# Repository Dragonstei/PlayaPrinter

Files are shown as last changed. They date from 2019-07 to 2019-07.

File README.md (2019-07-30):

# Playa Printer
You can find our project on: https://playaprinter.stadslabrotterdam.nl/

## The Idea

5 years ago Arnold Roosch, then a lab manager at Stadslab Rotterdam, came up with the idea to build a huge 3D dust printer to print objects out of sand at Burning Man Festival. Unfortunately, he wasn’t able to finish his project due to illness. Stadslab Rotterdam decided to continue the building of the printer with the help from friends and family of Arnold, lab employees and students from Rotterdam University of Applied Sciences.

## The Playa Printer

We aim to build a 3D sand printer to create sculptures that can be fully degraded and upcycled after a few days. The “Leave-no-trace” principle of Burning Man Festival is our inspiration. At the International FabLab Conference (FAB15) in Egypt we will be printing with desert sand. Because of the heat and wind the sculptures will dissolve in a few days. 

It is an ongoing project that will be improved and used with different materials by different groups of students.

### Resources:
* https://reprap.org/wiki/RAMPS_1.4
* http://www.geeetech.com/wiki/index.php/Ramps1.4

### Technical information:

Printer unique ID:
6b82af56-c7b9-41e2-99fa-451697f835ac

Stepper motor pin layout (A4988):\
2B = Black\
2A = Green\
1A = Red\
1B = Blue

**Make sure to redefine the steppermotor in configuration.h!**\

**Currently obsolete, printer does not have a screen connected**\
Make sure to download the latest NewLiquidCrystal library here and include it in Arduino:\
https://bitbucket.org/fmalpartida/new-liquidcrystal/downloads/

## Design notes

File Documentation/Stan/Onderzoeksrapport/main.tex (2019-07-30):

\documentclass[12pt, a4paper]{article}

\usepackage[english]{babel}
\usepackage[utf8]{inputenc}

% Skip to next paragraph on whiteline
\usepackage{parskip}

% Define bounds where text can be drawn
%\usepackage[top=100pt,bottom=100pt,left=75pt,right=75pt]{geometry}

% Headings
\usepackage{fancyhdr}
\pagestyle{fancy}
\fancyhf{}
\lhead{Research Playa Printer}
\rfoot{Page \thepage}

% Colors and links
\usepackage{color}
\definecolor{blue}{rgb}{0,0.5,1}
\usepackage{hyperref}
\hypersetup{
	colorlinks = true,
	linkcolor = blue,
	urlcolor = blue,
	citecolor = blue,
}

% Enable images
\usepackage{graphicx}
\usepackage{float}
\graphicspath{{images}{../images/}}

% Bibliography package
\usepackage[numberedbib]{apacite}
\bibliographystyle{apacite}

% Load LaTeX subfiles
\usepackage{import}
\usepackage{subfiles}
\usepackage[subpreambles=true]{standalone}

% Titlepage
\title{\textbf{Research paper Playa Printer\\Project 7/8}}
\author{Stan Boer, 0931006}
\date{\today}

%Examples:
%This is an example citation \cite{example}

\begin{document}
	\clearpage
	\maketitle
	\thispagestyle{empty}
	\newpage

	\setcounter{page}{1}
	\newpage
	
\section{Summary}
The aim of this research paper is to take a closer look at the options to automate the process of mixing clay and supplying that to our 3D printer. This to eradicate the manual labour and constant monitoring required for operating the printer.

To look at our available options, we'll take a look at what other companies, such as WASP and Italian inventor Enrico Dini, have accomplished in the process of building their own printers. Community made printers are based on manually mixing their materials and putting those in containers, so this is something that will not be covered in this research.

At the end of this paper we will elaborate on our findings, and explain why our goal is not achievable within our current scope.
	\newpage
	
	\tableofcontents
	\newpage
	
\section{Introduction}
The initial goal for the project is to build a 3D printer which will be able to print with a mixture that consists out of sand and a form of glue or epoxy, the Playa Printer. The plan with the current prototype is to print with a self-made clay mixture, as this is the most accessible to us. This mixture has to be made either by hand or be mixed by a machine. This second option would eliminate the effort required to mix the clay ourselves. This machine is supposed to be constantly running, getting the clay mixture ready to be transported to the extruder. This will eliminate the need to manually refill the printer every time the extruder is out of clay.

As this is a far more convenient option for a printer of our scale, we'll be looking into options on how to tackle this idea. This research paper will cover what options there are, show research done on the subject and a conclusion in which we will decide what prototype to build.
\begin{figure}[H]
	\centering
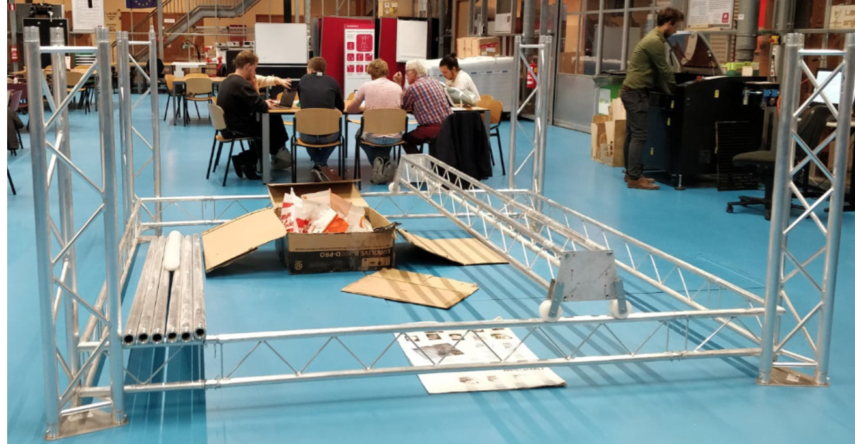
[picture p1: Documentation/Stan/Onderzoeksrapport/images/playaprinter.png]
	
	\caption{Playa Printer}
\end{figure}
	\newpage

\section{Research}
As the size of the printer is 3 by 3 meters, we will be needing a lot of material to be able to print at a scale like that. With existing 3D sand printers, the current method is to fill containers with the required mixture to be able to print with, and replace it every time the container is empty. For our project this can become quite inconvenient, which is why we will look in to figuring out a way of making this process more accessible. 
	
A company which created a similar 3D printer to ours, is called WASP. (reference) They created the Big Delta 3D printer, designed to be able to print with locally available materials at low cost. Their materials include mud combined with straw, and they are looking into the option to print with clay. They use a pugmill to combine their materials to be used as filament. When the extruder is empty, by the looks of it, the material has to be manually put into the extruder so that it can print again.
	
Unfortunately, there aren't any other companies working on a 3D printer of this scale. There are quite a few community made clay printers on small scale, so we can use that as a resource. Our aim will be to find a way to automatically mix our material together, and preferably pushes that to the extruder without requiring manual labour. The only effort required is to keep refilling the materials for the mixer. This situation would be close to ideal compared to what we are aiming for.

\section{Methodology}
Since 3D printing is picking up a lot of popularity, a lot more resources are available to us to develop a system on our down. To start, we'll have to look in to a different options on how to automate our mixing. Secondly, we'll have to compare the options, and pick one which we'll design a prototype for. 

To do an available product analysis, we'll be looking at the Big Delta printer from WASP and other companies who have attempted printing with sand. As the Big Delta printer is quite similar in design, it can be helpful in deciding our path to take. We'll be putting more priority on this specific printer than the other options. This will later be elaborated in the results.
	\newpage

\section{Results}
\subsection{Types of mixers}
\textbf{Hopper mixer}

Hopper mixers are an adaptation to mixers used for dough mixing, which consists of a horizontal shaft and either an open or lidded hopper. With this kind of mixer, dry material has to be added first and the liquid second. Some of thse mixers have the option to reverse the direction of the blades, so complete mixing can be achieved. Afterwards, the mixed clay has to be removed by hand and put in to the extruder.
\begin{figure}[H]
	\centering
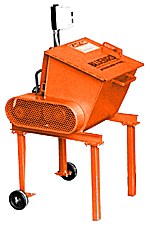
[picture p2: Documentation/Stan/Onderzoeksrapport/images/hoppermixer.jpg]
	
	\caption{Hopper mixer}
\end{figure}
	\newpage

\textbf{Soldner mixer}

Another form of mixers is a Soldner mixer, named after its designer. This mixer consists of a chain-driven rotating tub, with stationary bars on the inside, which allows the mixture to blend quickly and effectively. With this mixer it's normal to add the liquid first. After the dry material is added, it will be rotated through the stationary bars which chops and blends the clay for the desired consistency. This mixer also requires the material to be unloaded manually by hand and then stored.
\begin{figure}[H]
	\centering
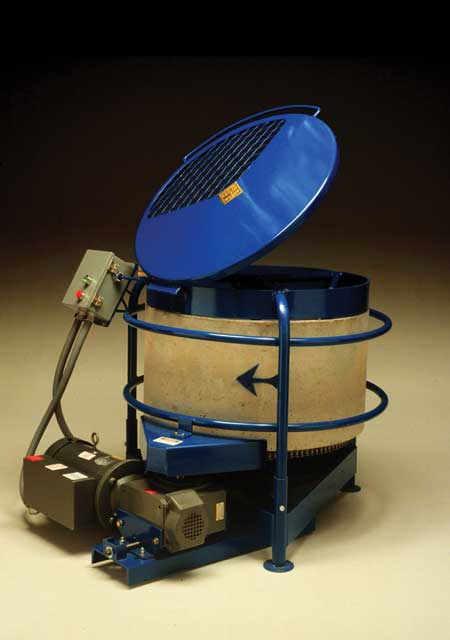
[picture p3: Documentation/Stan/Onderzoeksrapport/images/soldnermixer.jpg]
	
	\caption{Soldner mixer}
\end{figure}
	\newpage

\textbf{Pugmill}

Pugmills also work through a hopper and make use of a horizontal bladed shaft. The pugmill mixer requires moist clay to be put into the hopper which after blending gets extruded to a restricted opening at the end of a barrel. That means we are required to mix our material beforehand, which defeats the purpose of automating our process. Pugmills have the option to be equipped with a de-airing vacuum that can produce clay that is ready to be used, so that does give us an option of automation at the end of the process. 
\begin{figure}[H]
	\centering
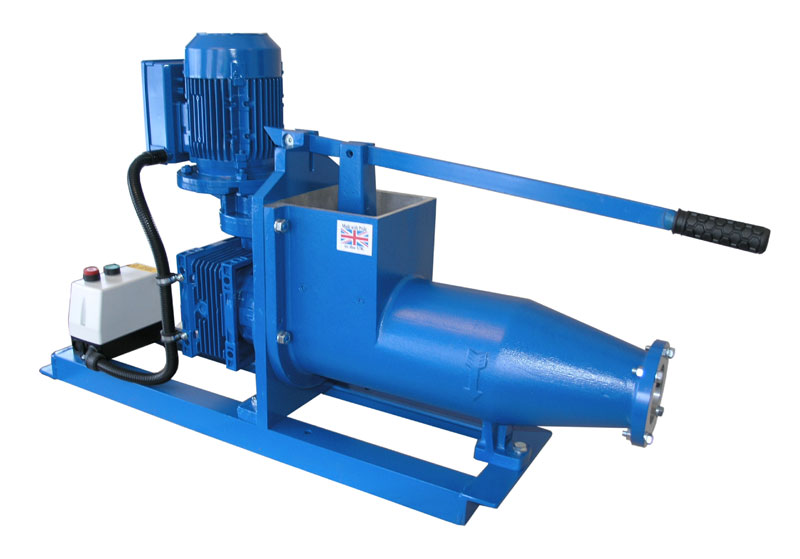
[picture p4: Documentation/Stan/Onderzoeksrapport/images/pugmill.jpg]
	
	\caption{Pugmill}
\end{figure}
	\newpage

\textbf{Mixer/pugmill}

Mixer/Pugmill combinations allow for both mixing clay and having a separate extruder for the material. The pugmill portion can serve as a discharge unit for the mixer, or as a separate pugmill on its own. The option of having a de-airing accessory will make it easier for us to automate the process of refilling the extruder.
\begin{figure}[H]
	\centering
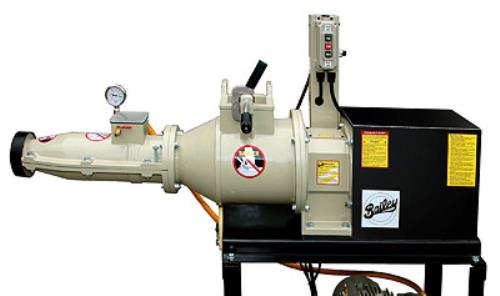
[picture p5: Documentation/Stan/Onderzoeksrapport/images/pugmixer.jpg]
	
	\caption{Mixer/pugmill combination}
\end{figure}
	\newpage

\subsection{Available printers}
To compare our available options, it is smart to look at what methods other companies use for their printers. Since there are only a few companies to look at, and most of them dont have their own resources available to us, our resources are quite limited to what we can find.

\textbf{Big Delta}

For our first example we will be looking at the Big Delta printer from WASP. They have built a 12 meter high printer, which they can use to print from locally available materials at low cost. Not much is known about their extruder. What is known just from pictures and videos from their demonstrations, is that they make use of an older pugmill. This mixer requires materials to be added to the machine, where it just keeps mixing the materials together untill it's ready for the extruder. It is also shown that the extruder needs to be manually refilled everytime, which can be quite some effort considering how high the printer can go.
\begin{figure}[H]
	\centering
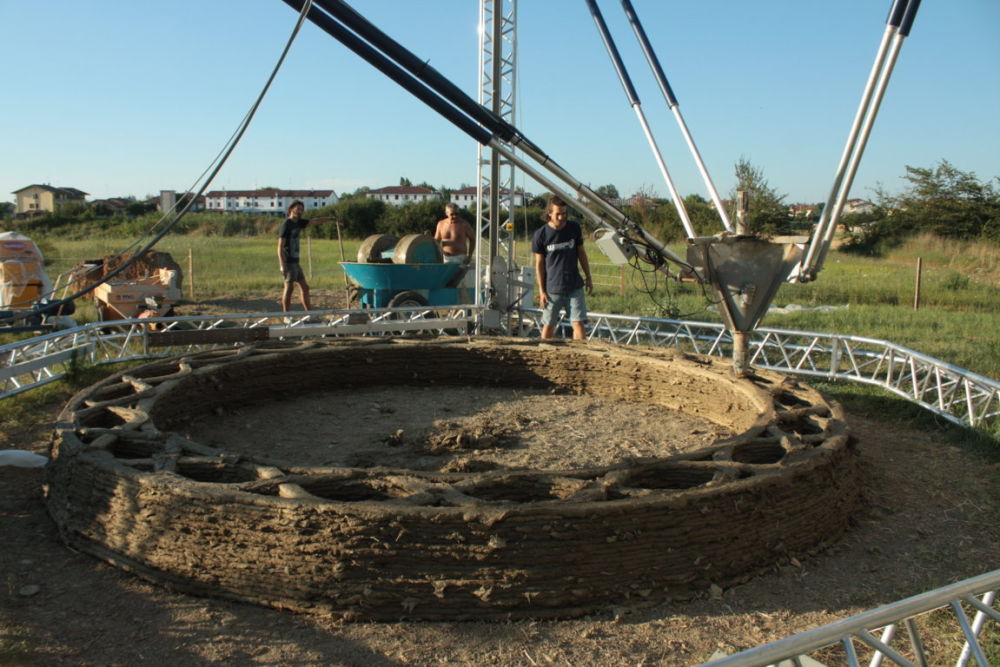
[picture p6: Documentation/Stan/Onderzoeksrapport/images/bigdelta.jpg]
	
	\caption{Big Delta printer using an older pugmill}
\end{figure}

This means that using an old hopmill and refilling manually still remaings one of our options, which is not really what we are looking for. It is unfortunate that they haven't gone towards automating this process, but this might still be a possibility for one of their future designs.
	\newpage
	
\textbf{D-Shape}
	
The D-Shape is a different kind of printer used than what we are working towards. This printer is effectively an up-scaled binder jetting process, where a binding material is dropped on each layer of powdered material. This method of printing is quite different than most orthodox 3D printers these days, is not really commercially available and would require us to completely rebuild our printer from scratch.
\begin{figure}[H]
	\centering
	
	\caption{D-Shape printer}
\end{figure}

Even though the frame is a lot more similar to our design compared to the Big Delta printer, the concept used for this printer is unfortunately not an option for us. The way this printer is controlled might be a point of interest for us, but for the sake of this research we will not be looking deeper into this. Development on the D-Shape has not been progressing a whole lot from what we know, so it's not worth to continue spending time on this printer for now.
	\newpage

\subsection{Comparison}
Now that we have our options listed and given a brief overview of what every mixer is capable of, it's time to put this in a morphological chart. This will help us in deciding which machine works best for our prototype. Since it is of no importance to us if we make use of a horizontal or vertical mixing shaft, we'll be leaving this out of our chart.

Because there are not really any available solutions for us to automate this process, we will have to come up with something ourselves based on the information gathered. That's why we'll only be looking at the side of automating our mixing process.

	\begin{tabular}{ | p{3.2cm} || p{2cm} | p{2cm} | p{2cm}| p{2.6cm} | }
	\hline
	\multicolumn{5}{|c|}{\textbf{Morphological chart}} \\
	\hline
	\textbf{Type} & Hopper mixer& Soldner mixer & Pugmill & Mixer/Pugmill \\
	\hline
	\textbf{Material} & Dry/ Wet & Dry/ Wet & Wet only & Dry/ Wet \\
	\hline
	\textbf{Starting price} & \$2,000  & \$6,000 & \$2,500 & \$5,000  \\
	\hline
	\textbf{De-airing} & No & No & Yes/No & Yes/No \\
	\hline
	\textbf{Unloading} & Manually & Manually & Manually/ Automatic & Manually/ Automatic \\ 
	\hline
	\end{tabular}

It remains quite difficult to make a proper comparison between our available options, as they are quite limited. We know that each one of these options gets the job done, but the focus remains on the unloading part. Preferably, we want the option to work with both dry and wet material, as we do not know beforehand what local materials are available. Any form of de-airing is welcome, as it will allow us to make the unloading and reloading into the extruder much more accessible.
	\newpage

\section{Conclusion}
Unfortunately, based on our research, the option to automatically refill containers is going to remain quite difficult. All of the available mixers still require manual unloading, while a few have the option to build an automatic system to refill on our own and attach it to the machine. Based on the scale of the printer and the scale of building such a system ourself, it is not smart to pursue this option for now. 

Since it is only the first protoype of this printer, it will become quite more difficult with the addition of a lot of moving parts, which can all influence the quality of the print and the weight of the printer itself. The option to manualy refill containers still remains, as the containers we use can be custom made with an adapter designed by ourselves. This should be done in combination with a de-airing unit, as this would immedietly get the material ready to be put into the containers.

Because of the price of these machines, it will be quite difficult for us to afford one. Our only options are that we either get one sponsored, or that we build one from scratch ourselves. Designing one would take a lot of research on its own, so it is best to pursue this at a later point in development if time permits.

No matter if we can get access to any of these mixers, or design one on our own, it is most advisable to look at a mixer/pugmill combination. A normal pugmill only works with wet material, which does not accomplish what we want to do. Both a hopper mixer and a Soldner mixer do not have the option of de-airing, which also defeats the purpose of our goal. Since we do not have a budget for buying one, we will start designing a prototype of a mixer/pugmill combination, to see what our options are and to see if we can accomplish the mixing on our own without having to make a huge investment.
	\newpage

	\nocite{*}
	\bibliography{main}
	\newpage

\end{document}

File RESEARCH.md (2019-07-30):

# Research

H-Bot to Core XY, to solve net torque issue\
http://www.doublejumpelectric.com/projects/core_xy/2014-07-15-core_xy/

Make Your Own Ceramic 3D Printer - Google+ info stream\
https://plus.google.com/communities/109375785524125994679

Open-source clay extruder\
https://www.thingiverse.com/thing:1413969

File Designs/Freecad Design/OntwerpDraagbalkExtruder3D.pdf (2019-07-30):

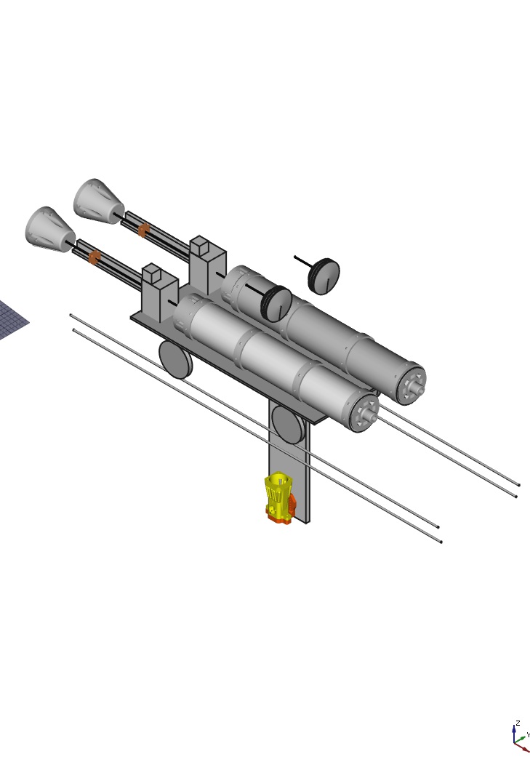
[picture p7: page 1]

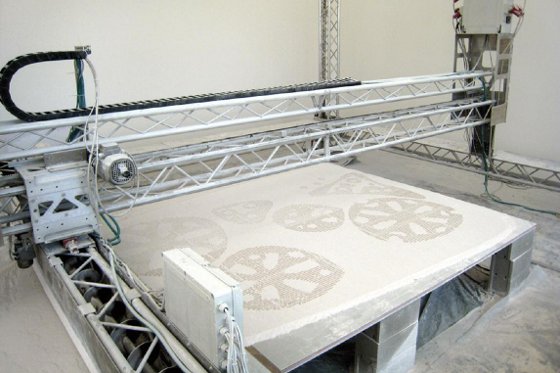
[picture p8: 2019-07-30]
Documentation/Stan/Onderzoeksrapport/images/dshape.jpeg

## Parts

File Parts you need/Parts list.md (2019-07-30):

| Item Description | Dimensions (mm) | Quantity  | Specifications  |
| --- |:---:| -----:|-----:|
| DT31-300 | 2000 x 50 x 50 | 10 ||
| DT33-150 | 1500 x 330 x 290 | 4 ||
| DT33-BPM | 310 x 280 x 45 | 4 ||
| DT22-C21V-L90 corner piece | 310 x 280 x 45 | 4 ||
| DT22-200 | 2000 x 220 s 35 | 4 ||
| DT22-300 | 3000 x 220 x 35 | 4 ||
| HDPE wheels with bearing | 84 x 45 | 16 ||
| HDPE wheels with bearing | 84 x 17 | 16 |  Hand made ||
| HDPE wheels with bearing | 84 x 60 | 8 ||
| Lead weights | 270 x 110 | 1 ||
| DT-20 Steelpin + safety pin | 70 x 5 | 40 ||
| DT-30 Steelpin + safety pin | 12 x 66 | 4 ||

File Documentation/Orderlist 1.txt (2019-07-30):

- 5 mm naar 5 mm kopeling stukje 
	https://www.123-3d.nl/123-3D-Flexibele-motor-koppeling-5-mm-5-mm-i340-t3045.html   €4.00	
OF
https://www.amazon.com/uxcell-Coupling-L30xD25-Flexible-Coupler/dp/B07G6PTMH2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 €10.00

- 4 amps driver stepper motor 3x verzamelboordje
https://www.amazon.com/gp/product/B06Y5VPSFN/ref=ox_sc_act_title_3?smid=AWQBCGWISS7BL&psc=1  

- juiste diammeter pijp voor extruder 
https://www.amazon.com/Small-Parts-Clear-Polycarbonate-Tube/dp/B003TJ9YI8

-  second t10 nut (for coupling leadscrew to plunger):
https://www.amazon.com/T10-Lead-Screw-Nut-10mm/dp/B07GBTSZ83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 €8.00

- Dubbelzijdige hittegeleinde tape voor de heatsinks 
- Slang extruder naar nozzle
- 3/8" x 3/8" push fit male adapter

- WormGearbox 20:1 of 30:1 :
https://www.amazon.com/gp/offer-listing/B06XGH6LHZ/ref=dp_olp_new_mbc?ie=UTF8&condition=new  €69.00 

https://www.youtube.com/watch?v=NVCXI3JaWYI
https://www.youtube.com/watch?v=wg2vw3aIFhI
https://forum.arduino.cc/index.php?topic=541983.0
http://www.airspayce.com/mikem/arduino/AccelStepper/MultiStepper_8pde-example.html
https://www.thingiverse.com/thing:831518
Clay recipe used:
35% kaolin
25% ball clay
20% nepheline syenite
20% silica

Add: deflocculant about 1% (sodium silicate, soda ash, or darvan 7)

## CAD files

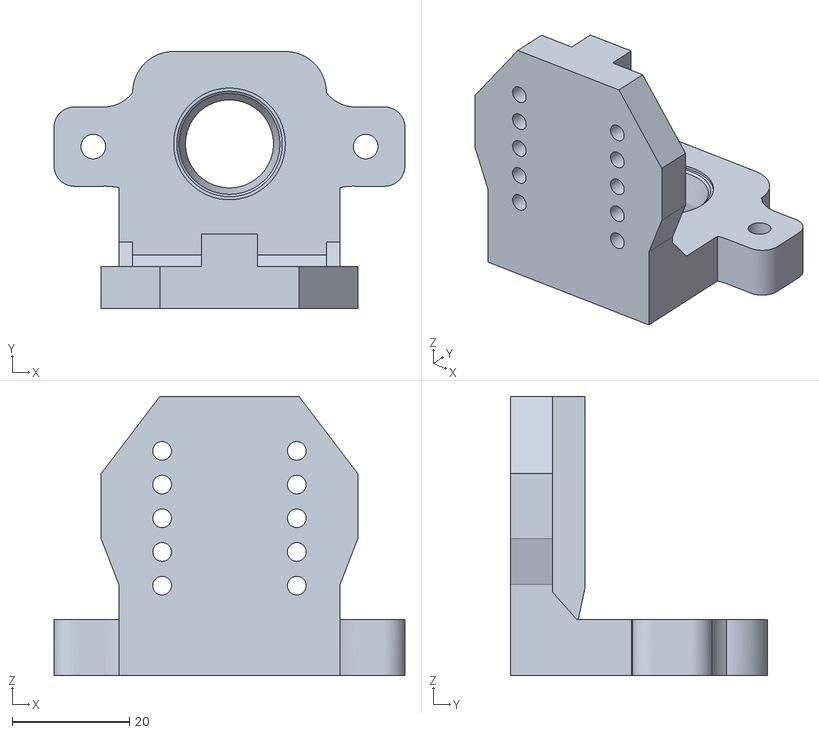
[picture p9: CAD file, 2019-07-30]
Designs/3D printhead/clay_extruder_mount.stl
59.9 x 43.9 x 47.7

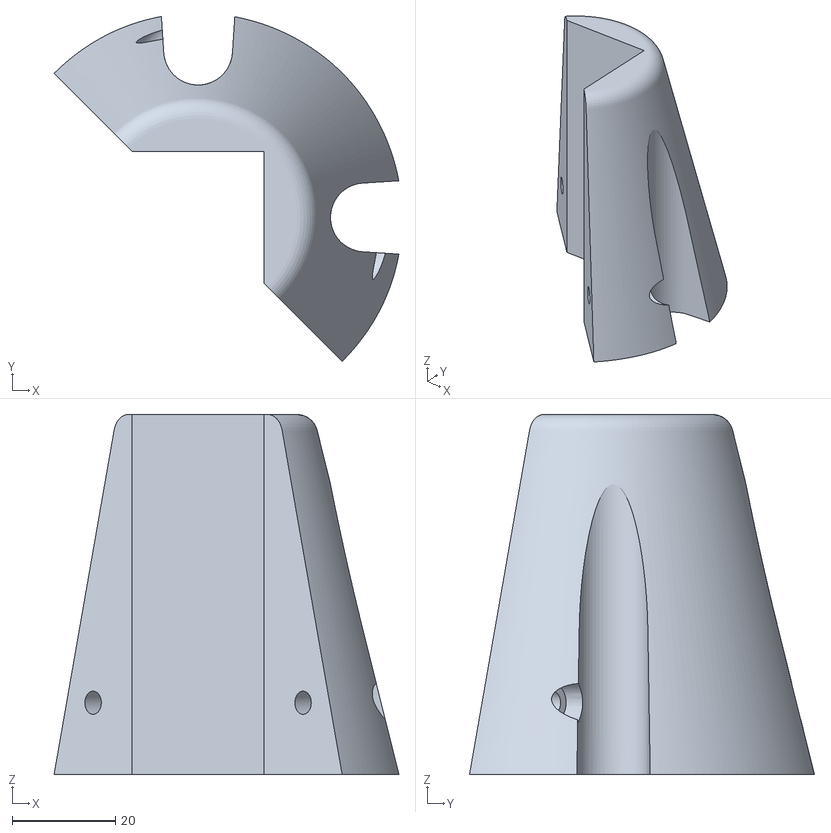
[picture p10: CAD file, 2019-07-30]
Designs/Clay extruder/guide_mount_B.stl
66.7 x 66.7 x 69.7

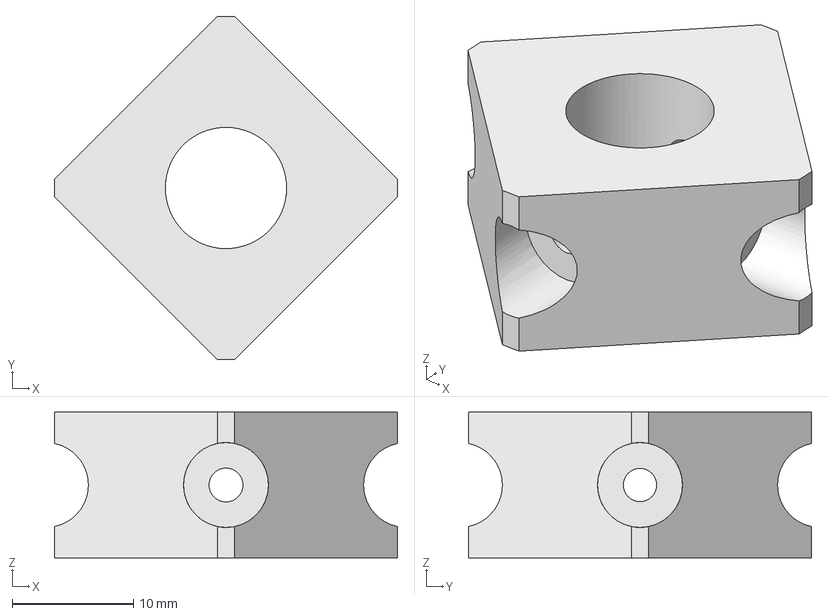
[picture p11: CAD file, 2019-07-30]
Designs/Freecad Design/OntwerpDraagbalkExtruder3D.FCStd
28.3 x 28.3 x 12.0 mm

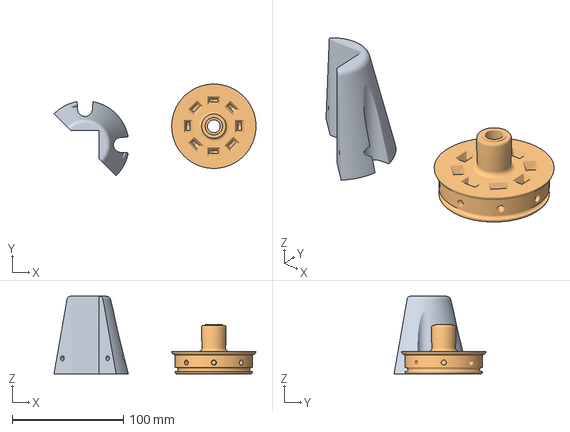
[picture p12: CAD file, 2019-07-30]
Designs/UM2_guide_mount_A.3mf
181.5 x 82.5 x 69.7 mm

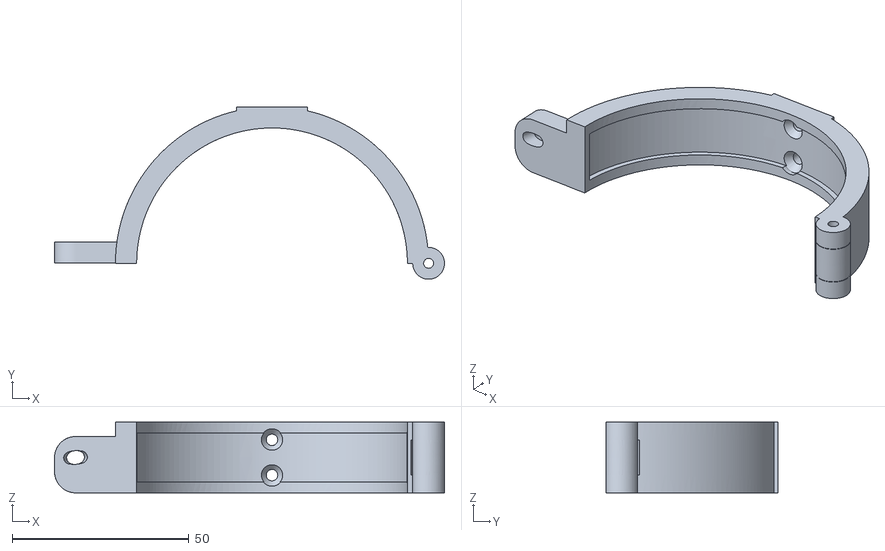
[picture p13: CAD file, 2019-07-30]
Designs/Clay extruder/extruderMount_A.stl
110.3 x 48.8 x 20.0

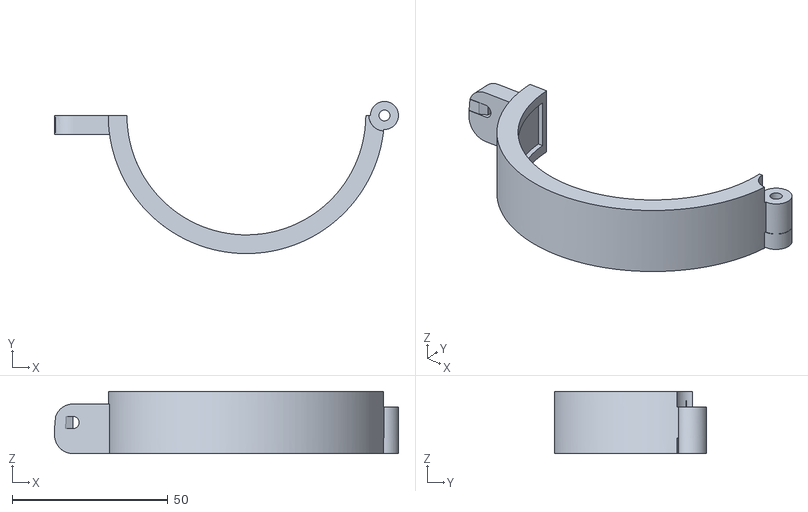
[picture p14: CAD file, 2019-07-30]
Designs/Clay extruder/extruderMount_B.stl
110.3 x 48.8 x 20.0

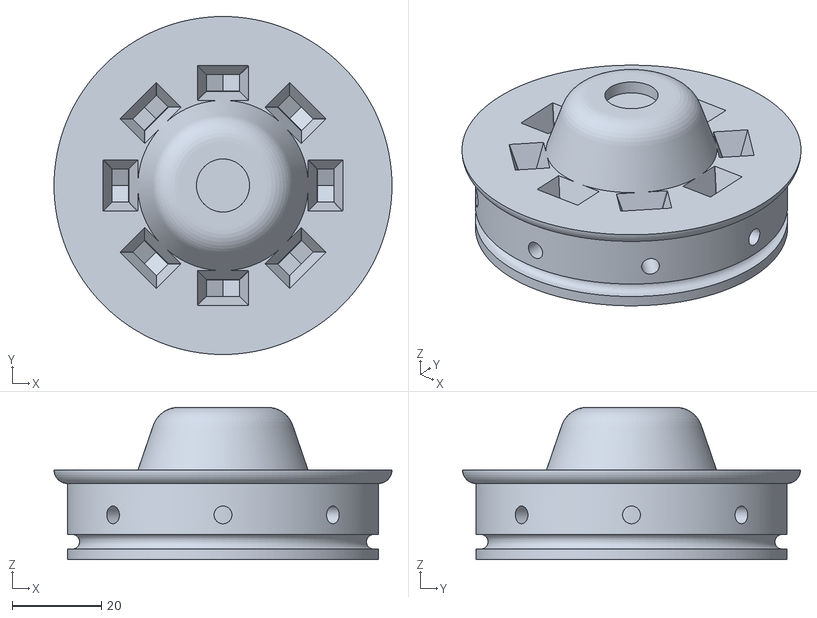
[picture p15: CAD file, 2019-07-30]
Designs/Clay extruder/nozzle_mount_type2_withSupport.stl
75.8 x 75.8 x 34.2

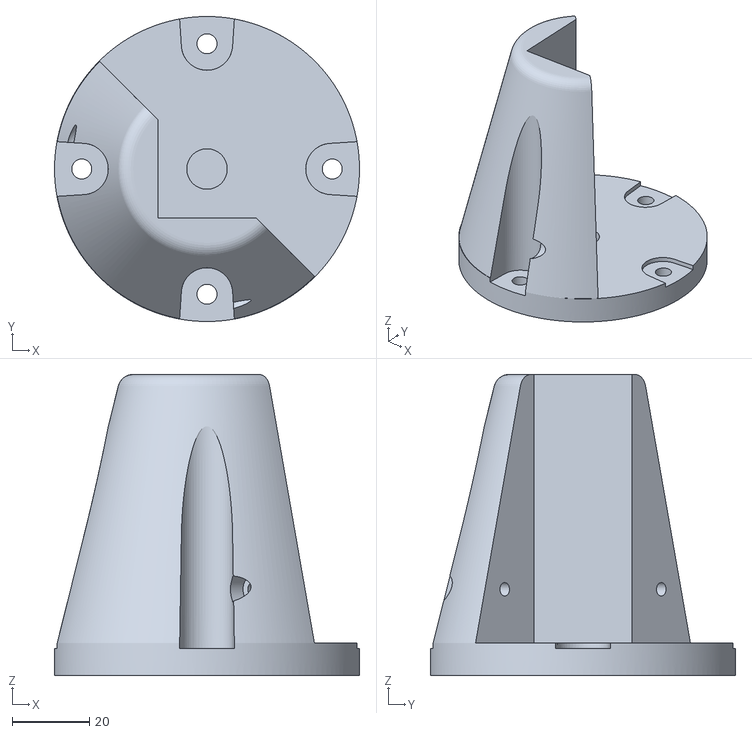
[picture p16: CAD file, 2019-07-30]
Designs/Clay extruder/guide_mount_A.stl
79.1 x 79.1 x 78.2

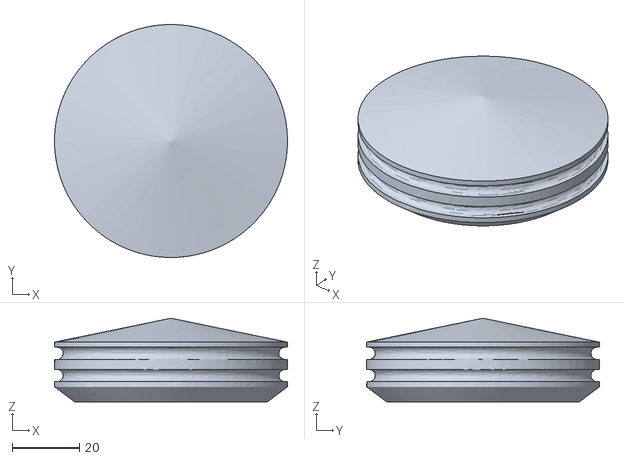
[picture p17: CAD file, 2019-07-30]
Designs/Clay extruder/plunger_withSupport.stl
69.0 x 69.0 x 24.8

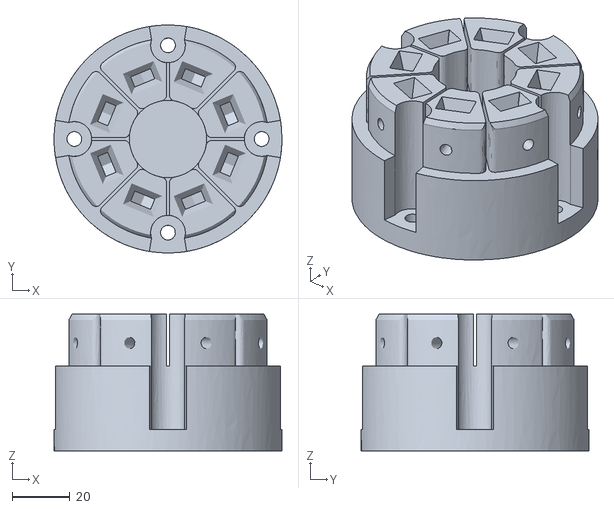
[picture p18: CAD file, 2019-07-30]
Designs/Clay extruder/tube_mount_withSupport.stl
79.1 x 79.1 x 47.5

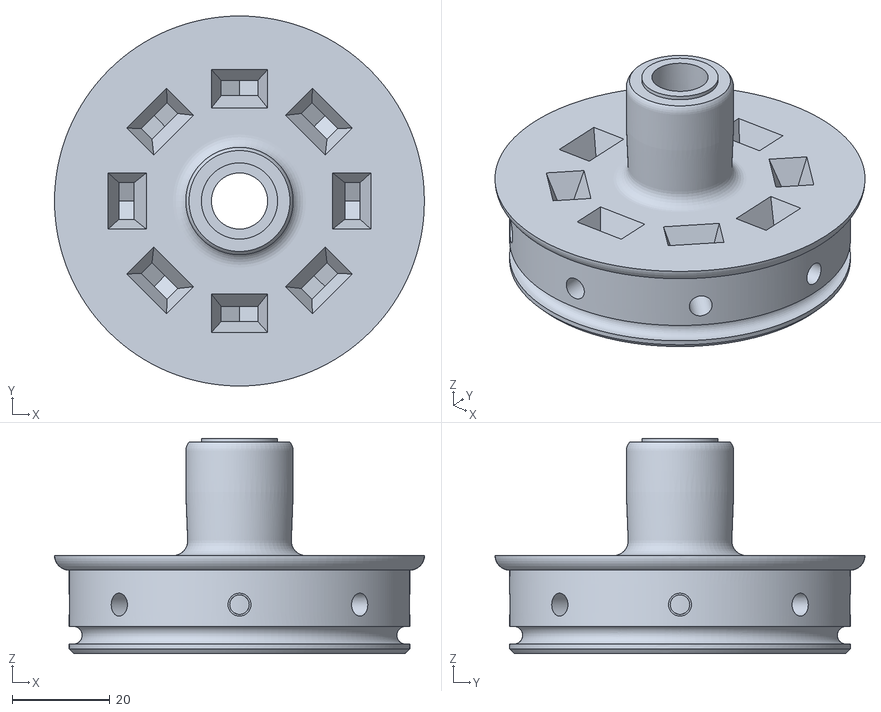
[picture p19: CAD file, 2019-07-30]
Designs/Clay extruder/nozzle_mount_type1.stl
75.8 x 75.8 x 44.1

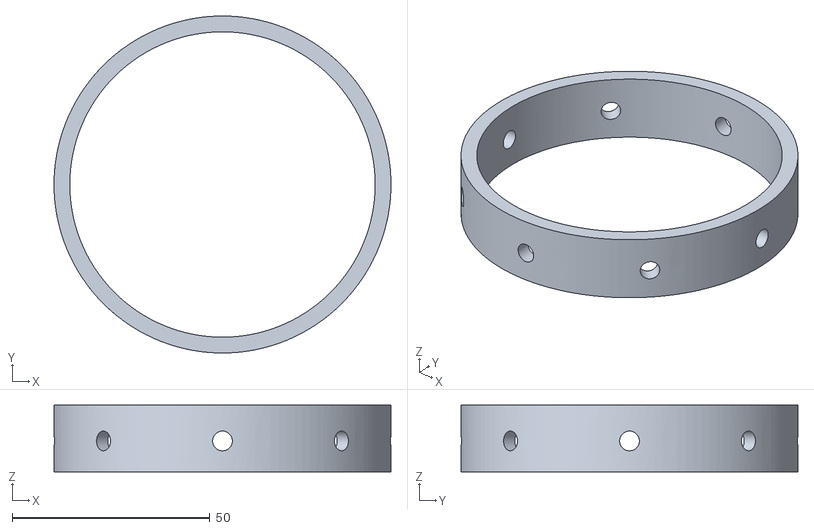
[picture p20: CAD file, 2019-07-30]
Designs/Clay extruder/drilling_jig.stl
85.2 x 85.2 x 16.9

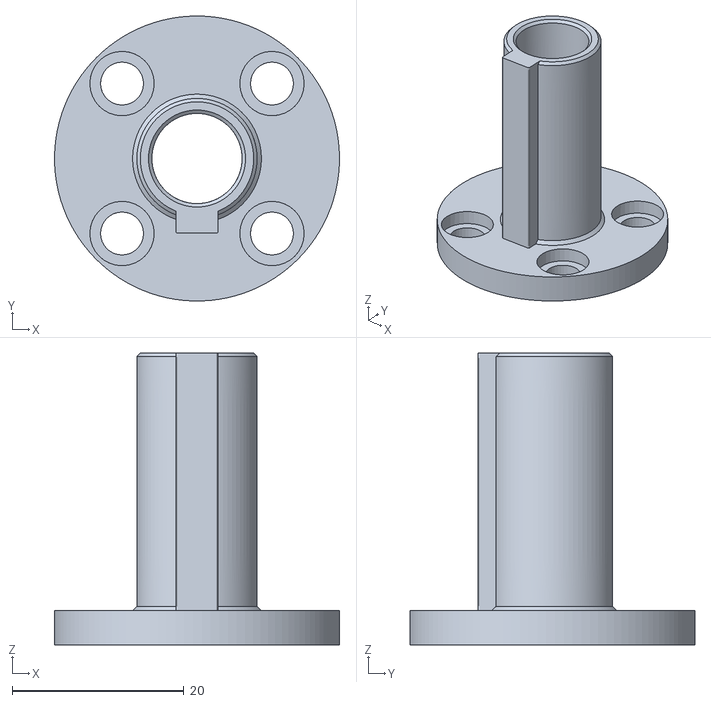
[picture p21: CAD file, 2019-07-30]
Designs/Clay extruder/nut_coupler.stl
33.2 x 33.2 x 34.0

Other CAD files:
Designs/Clay extruder/screw_guide.stl

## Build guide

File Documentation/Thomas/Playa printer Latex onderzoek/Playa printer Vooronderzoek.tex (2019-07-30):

\documentclass[11pt]{article} 

\usepackage{fullpage}
\usepackage[top=1.5cm, bottom=1.5cm, left=2cm, right=2cm]{geometry}
 \usepackage{array,multirow,graphicx}
 \usepackage{float}
 \usepackage{comment}
  \usepackage{xcolor}

\begin{document}
\title{Preliminary research Playaprinter 3D Nozzle}
\author{Thomas Martens Tia2}
\date{\today}
\maketitle

\begin{figure}[hbtp]
\caption{playaprinter}
\centering

\end{figure}
\newpage

\tableofcontents

TO DO: bronnen plaatsen\\
		Onderzoek naar Endstops als extra hoofdstuk????
		onderzoek naar 8 bit vs 32 bit controllers

\newpage

\section{Introduction Playa Project//ISSUE/Probleemstelling}
In our daily lives we use normal printers that can print the design on a flat surface, a 3D printer and  a ordinary  printer  working  principle  is  basically the  same, just  some  different  printing materials. Printing material  for a ordinary  printer  is ink  and  paper. A 3D  printer can be equipped  with metal, ceramic, plastic, sand and  other  different  print  materials.  The  printer  is  connected  to  the  computer through  USB/Bluetooth through which it prints layers of material. The methods generally referred to as 3D printing is called fused deposition modeling(FDM).\\

In this research paper  we shall examine the feasibility of creating a 4 by 4 meter 3D printer. This project is a collaboration between the Hogeschool Rotterdam and Havenlab RDM. It started at a Burning Man Festival with the idea to create a 3D printer that would "leave no Trace". The components of the Playaprinter needed to be crafted of parts that are available to the general public. Furthermore the design/code needs to be based off FOSS(free and open-source software). The "Leave no Trace" refers to the fact that the 3D printer could use natural resources like clay to create structures/sculptures. \\

Against this background, the central question that motivates this paper will be if it is possible to create a open source 'DIY' print nozzle. It is the most crucial part for creating precise 3D structures. In this paper we look at the different kind of 3D printer nozzles and how the work. In addition if it is possible to create a 3D printer nozzle and other needed materials that are available to the general public.  \\

\newpage

\section{Different materials used in 3D printing}	
One of the most crucial factors in creating your own 3D printer is knowing the type of material being used. This determines the 3D head that is needed to transport/heat the substance. To answer this question, we begin by taking a closer look at the different kind of materials. 

\subsection{ABS - PLA - PTG}
			
	The most common type of 3D print material found in almost every consumer device. It is easily  accessible and works well in different situations depending on the type 3D filament. Some filament can make a 3D structures flexible while others filaments excel at strength and pressure. ABS was one of the first plastic to be used with 3D printers. Many years later, ABS is still a very popular material thanks to its low cost and good mechanical properties. ABS is known for its toughness and impact resistance, allowing you to print durable parts that will hold up to extra usage and wear.  \\
	
\begin{figure}[hbtp]
\caption{Common 3D printer material}
\centering
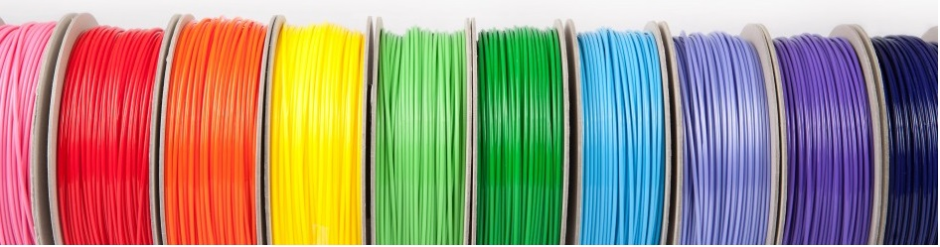
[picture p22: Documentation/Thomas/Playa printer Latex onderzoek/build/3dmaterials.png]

\end{figure}

\subsection{Algae}    
	Algae is a new 3D print material first proofed by researchers at the Wageningen University. Working with scientists, Klarenbeek  developed a new way of 3D printing with living organisms. The created a 3D printed chair using living fungus, which then grows inside the structure to give it strength.  A different version of this is growing algea and than process the algae into a special sustainable filament.\\
	
	\begin{figure}[hbtp]
	\caption{Algea \& 3D Filament}
	\centering
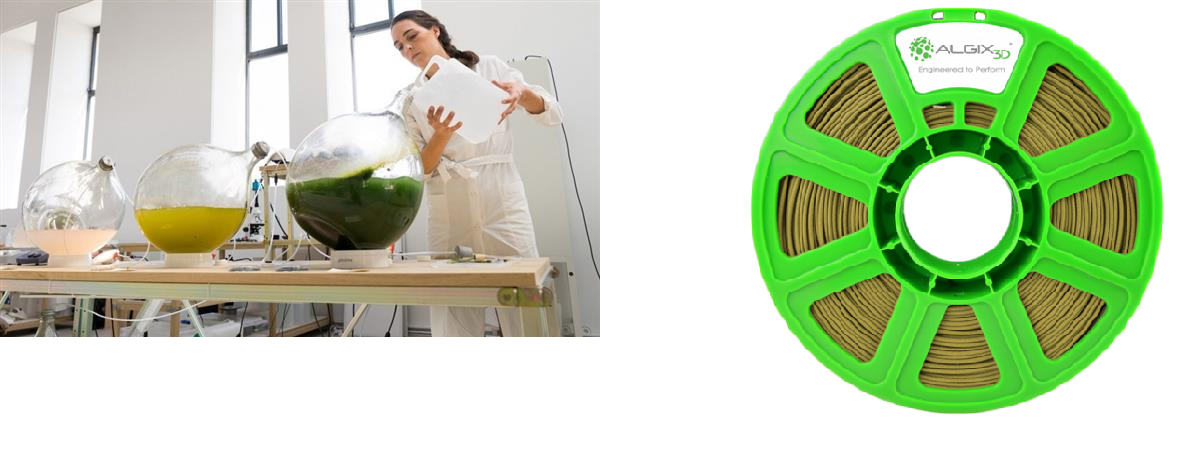
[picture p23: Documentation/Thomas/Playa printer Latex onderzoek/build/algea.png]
	
	\end{figure}
	
\newpage

\subsection{Clay and other  sand combinations}

	 Clay is a common resource that can be found almost anywhere, it is a finely-grained natural rock or soil material that combines one or more clay minerals. Clay are plastic due to particle size and geometry as well as water content. A property of clay is that it become hard, brittle and non–plastic upon drying or heating. In the natural environment a lot of different combinations of sand, silt and other materials can be found. Clay is distinguished from other fine-grained soils by differences in size and mineralogy.\\
	
	\begin{figure}[hbtp]
	\caption{Building Clay \& Natural Clay }
	\centering
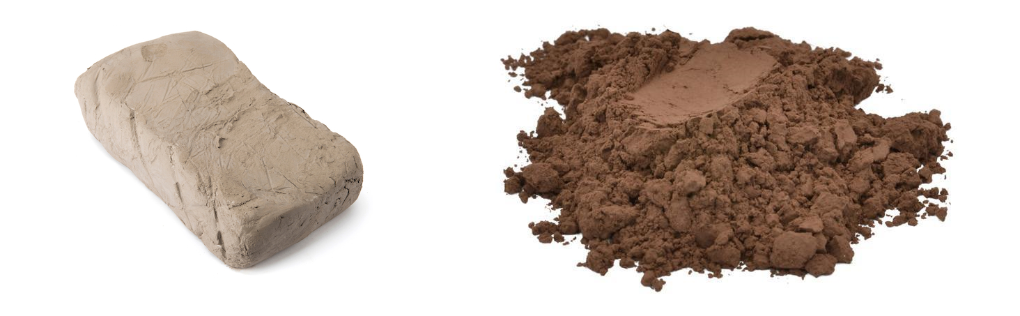
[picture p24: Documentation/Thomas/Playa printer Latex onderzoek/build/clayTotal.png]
	
	\end{figure}

	\subsection{Metal powders}
		Metal 3D printing is carried out by fusing powdered metal particles together to create a object in a successive layer by layer printing process. Metal is heated up and requires specialized equipment to create special 3d metal powder. A powder bed fusion 3D printer uses a laser to sinter powdered material. A powerful laser beam selectively melts and fuses tiny powder particles together. Once a layer is finished, more powder is rolled and spread onto the print bed. The particle properties of the metals is very important for successful 3D printing.\\

\begin{figure}[hbtp]
\caption{Metal Powder}
\centering
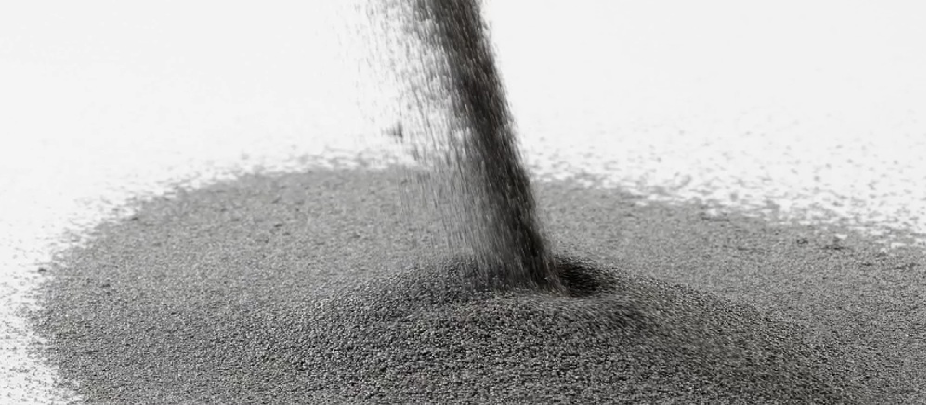
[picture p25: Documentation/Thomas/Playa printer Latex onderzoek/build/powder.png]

\end{figure}

\newpage

All these different types of materials require a specific type of 3D nozzle + extruder combination to work. ABS \& Alga and other common filament uses a more traditional hotend to create 3D objects.  For clay and other natural resources this usually  requires a auger design with a fluid pump to work correctly. This is due to the fact that it needs a container and controlled pressure.\\

Industrial installation uses metal powder to use as a base material for printing. In the next chapter the paper will look at the different kind of systems in greater detail.  

\newpage
\section{Printhead}

In this section we will look at the different 3D nozzle \& extruders combinations and the working principles behind them. Our focus is on the possibly to replicate it with normal means and being applicable for the (PlayaPrinter) 4m by 4m printer. 

\subsection{Hotend Design}

The hotend the is most common used in a 3D printer. The hotend is where the heated filament comes 
out and moves through the nozzle to the print bed to create a 3D object. The heaterblock is the part that is responsible for heating up the filament. ABS needs to be around 230 degrees to start to liquefy. During the liquefaction stage the filament is compressed in smaller space to increase heat friction. Temperature control is a big factor for creating good 3D print results. 

\begin{figure}[hbtp]
\caption{Hotend }
\centering
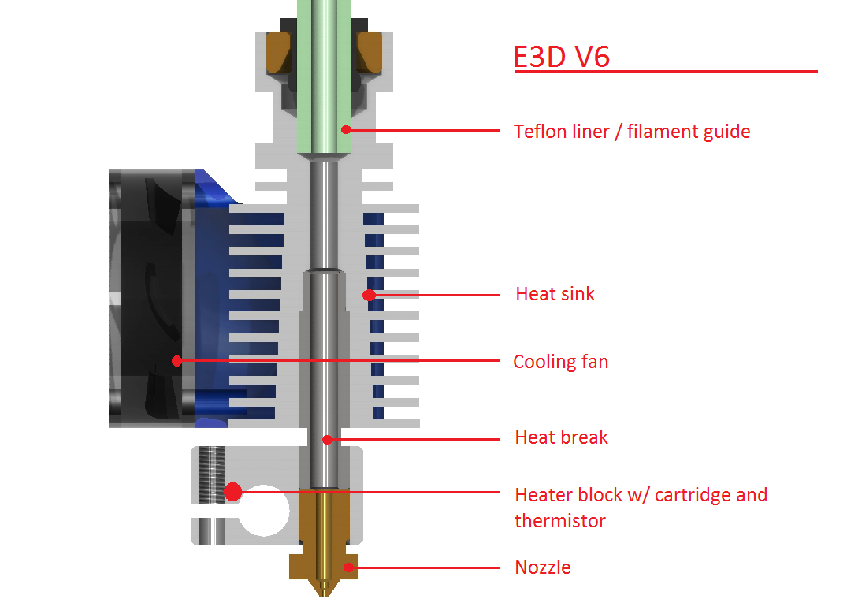
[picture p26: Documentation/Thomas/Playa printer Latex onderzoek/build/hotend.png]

\end{figure}

\subsection{Stereolithography  } 
The stereolithography  process first appeared in the early 1980s, when Japanese researcher Dr. Hideo Kodama invented the modern layered approach to stereolithography by using thin layers of a material curable by ultraviolet light. A process by which light causes chains of molecules to link, forming polymers.

  Today it is still one of the most popular method for designers. The finished parts have a very high resolution and accuracy, clear details and the smoothest surface finish of all plastic 3D printing technologies. Futhermore  the advantages of stereolithography is its speed, functional parts can be manufactured within a day.

\begin{figure}[hbtp]
\caption{Stereolithography}
\centering
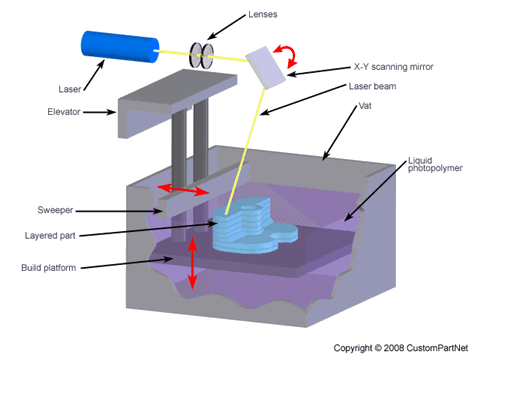
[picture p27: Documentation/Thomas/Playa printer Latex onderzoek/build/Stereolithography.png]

\end{figure}

\subsection{Powder Bed Fusion}
Selective laser sintering (SLS) was one of the first additive manufacturing techniques, developed in the mid-1980s by Dr. Carl Deckard and Dr. Joe Beaman at the University of Texas at Austin. Their method has since been changed to work with a larger range of materials. This include plastics, metals, glass and other composite material powder. Today this is called Powder Bed Fusion. \\

Power bed fusion is the most common additive manufacturing technology for industrial applications. It starts by using a atomizer. Atomisation is the process of transforming a solid solution form into fine particles in a surrounding gas.  The end result is a powder which than can be used for 3D printing. \\

Industrial power bed fusion systems use a single or multiple high-power carbon dioxide lasers. Powder is dispersed in a thin layer on top of a platform inside  the build chamber.
The printer preheats the powder to a temperature just below the melting point. This makes it easier for the laser to raise the temperature of specific regions of the powder bed as it traces the model to solidify a part. This fuses the particles together mechanically to create one solid part.\\

It is most used in very specialized facilities and has very specific requirements to work properly though it is superior in its strength and for creating very large objects.  \\

\begin{figure}[hbtp]
\caption{Powder Bed Fusion}
\centering
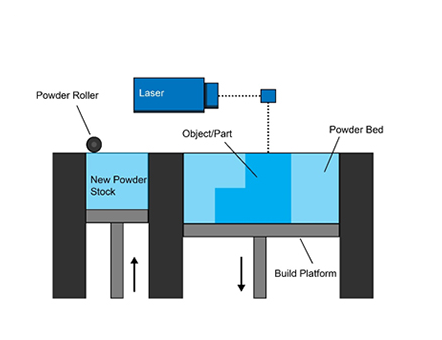
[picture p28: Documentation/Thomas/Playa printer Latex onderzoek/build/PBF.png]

\end{figure}

\newpage

\subsection{Auger Design}

A auger design is based on the principles of the Archimedes screw. It is a machine  used for transferring water from a low-lying body of water into irrigation ditches. Water is pumped by turning a screw-shaped surface inside a pipe.  This technology has been around since Egyptian times, when it was used to remove water from the Nile river.\\

 An auger design uses a screw (auger) to move material down a cylinder. The rotation of the screw creates a shearing force on the material which drives it down the threads of the screw. A example of a 3d print auger design is shown below.\\
 
 \begin{figure}[hbtp]
 \caption{Auger}
 \centering
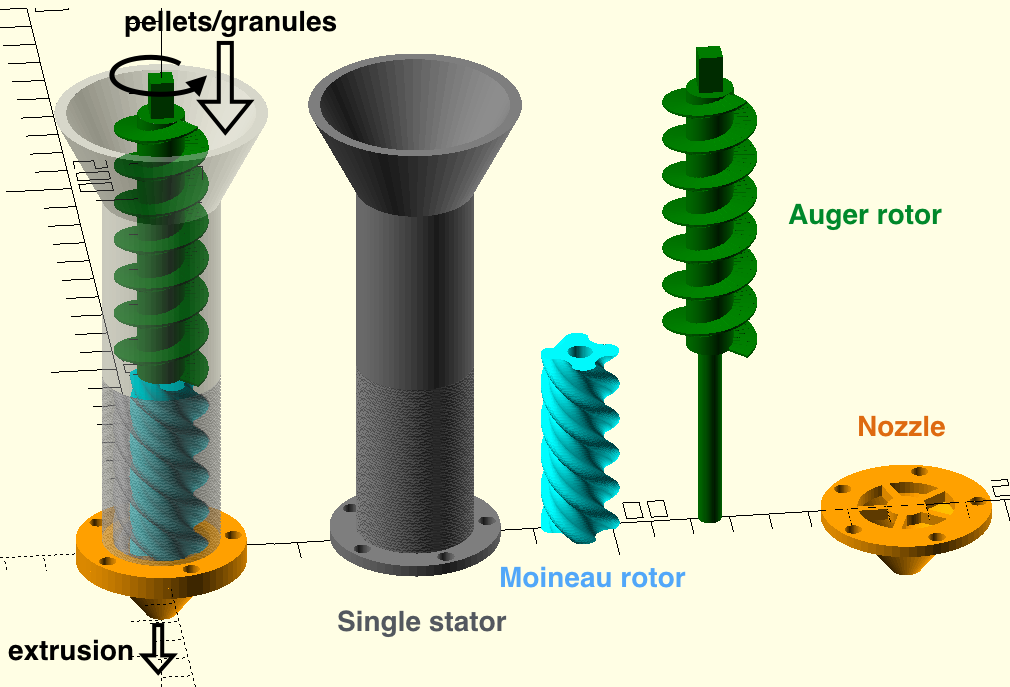
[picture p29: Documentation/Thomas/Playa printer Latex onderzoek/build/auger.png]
 
 \end{figure}

  \subparagraph{Types of screw}
 There are many variations in the design of the screw which are fundamental in moving the fluid through. The primary differences consist of the number of intermeshing screws involved, the pitch of the screws, and the general direction of fluid flow. A single screw pump contains a single screw that rotates within a closed tube. The individual screw pushes a set volume of fluid forwards with every rotating. Two screws or more can benefit a precise flow rate but  come at the expense of high cost and additional maintenance. 
\\
 \begin{figure}[hbtp]
 \caption{Screw design}
 \centering
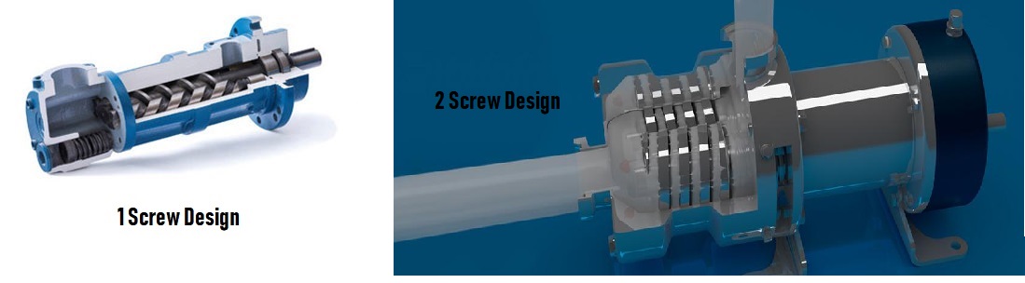
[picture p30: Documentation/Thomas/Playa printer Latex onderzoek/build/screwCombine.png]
 
 \end{figure}

\newpage

\subsection{Auger Design + Fluid Pump Extruder}

 The  characteristics  of a fluid  pump  is  that by  adjusting  the  motor speed  you can control  the flow rate. It works by having a closed tube with at the end a cover which creates a airtight seal. This cover is connected to the motor which pushes it down through the tube.\\
 
  As the material is pushed down it comes in contact with the screw, which turns for a set length of time or rotates at a specified speed.  The screw is causing the material to move down the threads. As the material reaches the end of the nozzle the pressure  increases. This is due to the fact that the  flow  encounters resistance due to the restriction in area at the nozzle.\\
  
Any area restriction such as at the output of the auger creates backflow. The amount of backflow is proportional to the pressure drop from the nozzle to the extruder. As long as the the pressure inside the system is stable, the flow out of the needle is equal to the rotorspeed flow minus the backflow.   \\

With this design it is very import to control the pressure inside the system. 

\begin{itemize}
	\item Low Air pressure
	\begin{itemize}
		\item screw will cavitate
		\item create missed dots
		\item inconsistent 3D objects
	\end{itemize}
\end{itemize}

 \begin{itemize}
	\item High Air pressure
	\begin{itemize}
		\item Material will be forced through
		\item drool(excess of fluid)
		\item inconsistent 3D objects
	\end{itemize}
\end{itemize}

\begin{figure}[hbtp]
\caption{Auger \& Extruder}
\centering
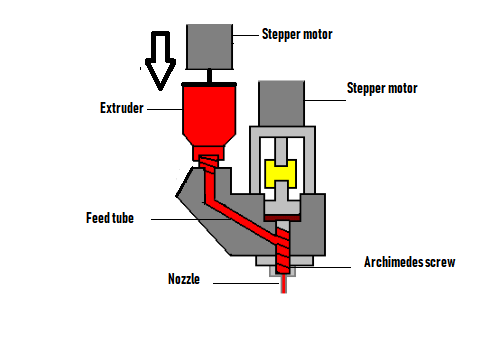
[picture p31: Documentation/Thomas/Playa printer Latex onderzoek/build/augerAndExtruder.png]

\end{figure}

 \newpage
 \section{Motors}
	In this part of preliminary research we will look at the different kind of motors available. Every printer needs motors for the x \& y \& z  axis, futhermore the 3D printhead/extruder needs depending on the type also 1 or more motors. \\
	
	\subsection{Brush motor}
 		The DC brush motor is one of the simplest motors in use today. You can find these motors just about anywhere. They are in household appliances, toys, and automobiles. Being simple to construct and control, these motors are the go-to solution for professionals and hobbyists.\\
 		
 		If energy flows the windings are energized, they attract to the magnets located around the motor. This rotates the motor until the brushes make contact with a new set of  contacts. This new contact energizes a new set of windings and starts the process again.
 		
\begin{itemize}		
\item Pros
\begin{itemize}
		\item Simple to control
		\item Excellent torque at low RPM
		\item Inexpensive and mass produced
		\item Simple to control
	\end{itemize}		
\end{itemize}	

\begin{itemize}		
\item Cons
\begin{itemize}
		\item Brushes can wear out over time
		\item Brush arcing can generate electromagnetic noise
		\item  Usually limited in speed due to brush heating
	
	\end{itemize}		
\end{itemize}		

\begin{figure}[hbtp]
\caption{Brush motor }
\centering
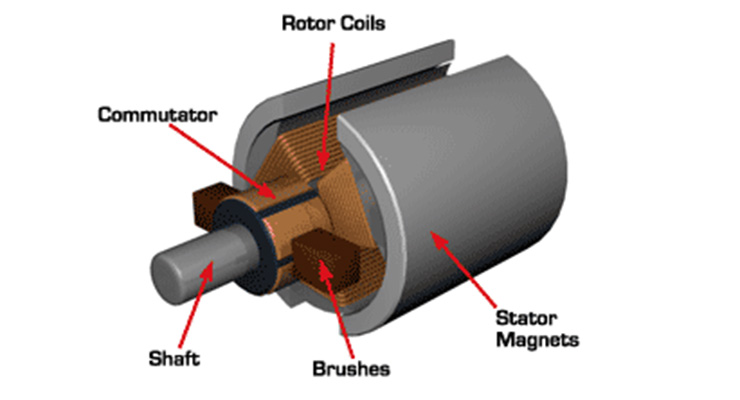
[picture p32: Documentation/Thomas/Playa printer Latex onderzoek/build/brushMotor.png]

\end{figure} 		

\newpage

	\subsection{Brushless motor}
Brushless motors have begun to dominate the hobby markets between aircraft and ground vehicles. Controlling these motors was until a few years difficult due to the fact that controllers were buggy and expensive. Nowadays micro controllers are cheaper and powerful enough to handle the task. Without brushes to fail, these motors deliver more power and can do so more silently.\\

The mechanics of a brushless motor are simple. The only moving part is the the rotor, which contains the magnets. Where things become complicated is orchestrating the sequence of energizing windings. The polarity of each winding is controlled by the direction of current flow. 

\begin{itemize}		
\item Pros
\begin{itemize}
		\item Reliable
		\item High speed
		\item Efficient
		\item Mass produced and easy to find
	\end{itemize}		
\end{itemize}	 

\begin{itemize}		
\item Cons
\begin{itemize}
		\item Difficult to control without specialized controller
		\item Requires low starting loads
		\item Typically require specialized gearboxes in drive applications
	
	\end{itemize}		
\end{itemize}	

\begin{figure}[hbtp]
\caption{Brushless motor}
\centering
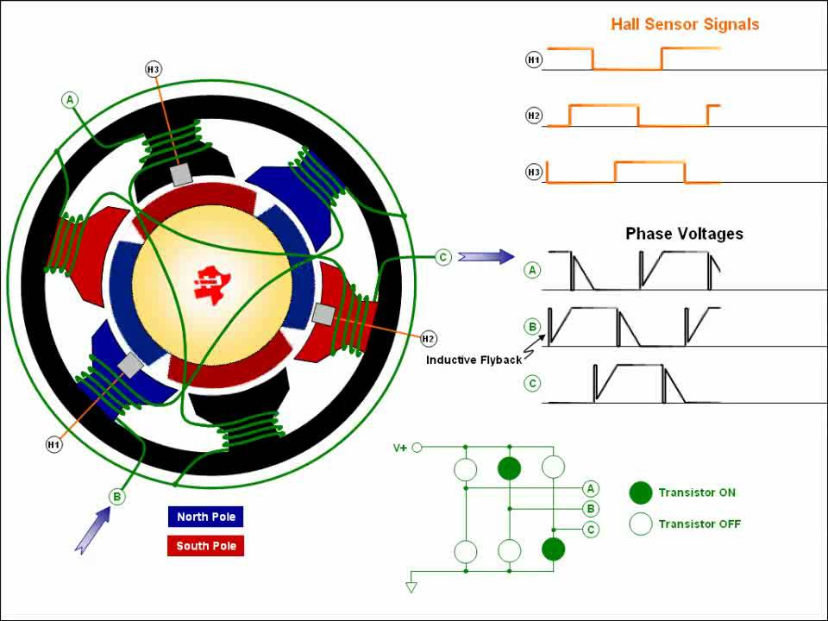
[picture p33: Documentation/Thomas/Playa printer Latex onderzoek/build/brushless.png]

\end{figure}

\newpage

	\subsection{Stepper motor}
Stepper motors are  motors for position control. They can be found in desktop printers, plotters, CNC milling machines  and anything else requiring precise position control. Steppers are a special segment of brushless motors. They are purposely built for high-holding torque. This high-holding torque gives the user the ability to incrementally "step" to the next position. \\

Stepper motors behave exactly the same as a brushless motor, only the step size is much smaller. The only moving part is  the rotor, which contains the magnets. As with brushless motors the complicated aspect is orchestrating the sequence of the windings. 

\begin{itemize}		
\item Pros
\begin{itemize}
		\item Excellent position accuracy
		\item   High holding torque
		\item  High reliability
		\item   Most steppers come in standard sizes
	\end{itemize}		
\end{itemize}	 

\begin{itemize}		
\item Cons
\begin{itemize}
		\item Small step distance limits top speed
		\item    It's possible to "skip" steps with high loads
		\item    Draws maximum current constantly
	
	\end{itemize}		
\end{itemize}	
\begin{figure}[hbtp]
\caption{Steppermotor}
\centering
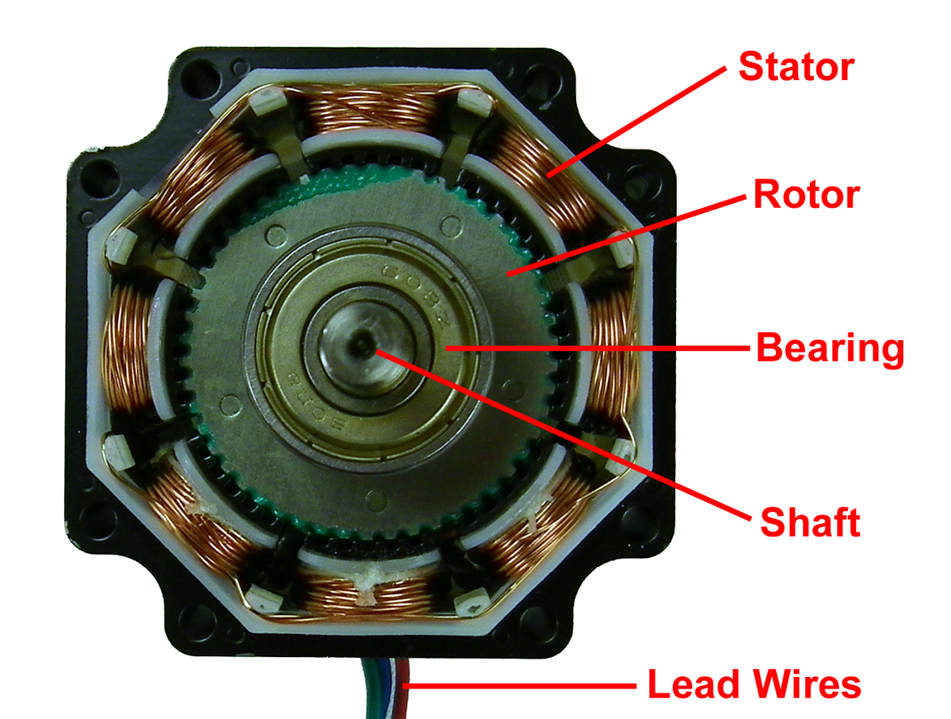
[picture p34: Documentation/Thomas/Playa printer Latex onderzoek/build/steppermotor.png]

\end{figure}

\newpage
\subsection{Linear motors }

A linear motor is often described as a rotary motor, just cut up and rolled out. Linear motors use magnetic levitation to move an object. This way it is not slowed down by friction and can actually achieve more precise control than mechanical options.\\

In a traditional electric motor, the rotor spins inside the stator. In a linear motor the stator is unwrapped and laid out flat and the "rotor" moves past it in a straight line. Linear motors have a number of advantages over ordinary motors. There are no moving parts to go wrong. As the platform rides above the track on a cushion of air, there is no loss of energy to friction or vibration. The same technique drives the Maglev trains.  

\begin{itemize}		
\item Pros
\begin{itemize}
		\item  Reliable
		\item  High speed
		\item  Efficient
		\item  No rotary to linear conversion required
	\end{itemize}		
\end{itemize}	 
 	
\begin{itemize}		
\item Cons
\begin{itemize}
		\item    Expensive
		\item    Require custom controllers
		\item    Purpose built for each system
	
	\end{itemize}		
\end{itemize}	
\begin{figure}[hbtp]
\caption{Linear motor}
\centering
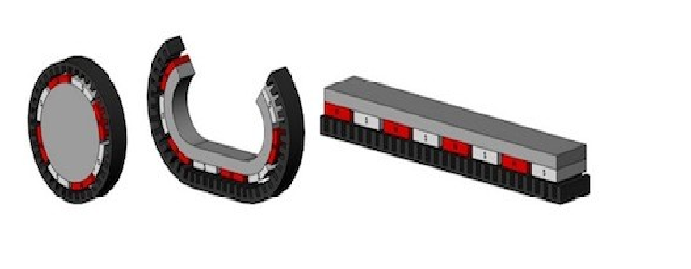
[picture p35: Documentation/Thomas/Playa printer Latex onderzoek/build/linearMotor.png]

\end{figure}

\newpage

\section{Morphological Chart}
 	
 	\begin{center}
Table 1. Morphological chart
\end{center}
 \begin{center}
 \begin{tabular}{|| c || c | c | c | c ||}
 
 \hline\hline
    \textit{Sub Functions} & \textit{Solutions} & \textit{Solutions}  & \textit{Solutions} & \textit{Solutions}   \\ [1.5ex]  
  \hline\hline
   
   \textit{3D head Type} & Stereolithography & Power Bed Fusion &  Auger + Extruder &  Hotend    \\
   \hline
    \textit{Motor} & Brush motor & Stepper motor & Linear motor & Brushless motor   \\
   \hline

 	\textit{Screw type} & 1 Screw &  2 screw & x & x  \\
   \hline   
   	\textit{3D printhead material}   & ABS/PLA & Metal casting & Aluminum & Wood     \\
   	\hline
   	\textit{Nozzle size}  & 0.6  & 0.8 &  1.2  & 1.5   \\
   	\hline 
   	\textit{Controller}  & Mega + RAMPS & Smoothieboard & Azteeg X5 GT  & RADDS   \\
   	\hline\hline 

 \end{tabular}
\end{center}  

\section{Are there already existing (partial) solutions to this problem? }
For the Playaprinter the  objectives are to create a massive 3D printer that can print with natural resources. The choice for this project is based on clay or other materials with a similar liquid properties. It needs to be fabricated with normal purchasable parts without resorting to expensive solutions. Furthermore it needs to print large 3D objects with a high level of detail.  \\

 Currently the are no (affordable) clay printer purchasable. The are a few clay nozzle sets and extruders but for a very steep price and with questionable performance. The also come bundled with closed software and are meant for small printing. \\ 
 
 So it will be required to make a custom solution that satisfies the needs for this project. This will include the 3D print head which receives the clay and hold the auger and motor. The nozzle will be attach to the bottom of the 3D head which will feed the clay. \\

 With regards to the other parts:
 
 	\begin{itemize}
 		\item Nozzle size
 		\item Controller
	\end{itemize} 	 
 
In these categories the are several parts available to purchase. It will be a combination of desk research and field research to determine the best combination of components. After this process the need to be combined through soldering and creating code for all the individual component necessary.
 \newpage

\section{Conclusion }

Playaprinter needs to be a printer that is able to print material over a large x \& y \& z axis, with a 3D head + nozzle that is capable to print clay with a high level of detail. \\

 The playaprinter will need a auger + extruder design to function correctly. This is because of the sheer pressure required to push the clay through.\\
 
  The extruder can push the clay in which the extruder is essential. In combination with a auger design it should be possible to print clay. The combination of a auger and extruder should ensure a system in which a double system of delivery  works together. The auger creates a high pressure zone in which the clay is pressed through the nozzle whilst the extruder controls the overall system pressure. \\

 With the combination of a auger and a extruder the accuracy of the 3D print should increase. It can solve outflow problems due to the fact that pressure inside is controlled and should result in a smooth and accurate 3D printed object. \\
 
It will require creating several custom 3D printed objects to craft all the necessary parts.   Also needed is a workshop to create and lay out all the parts.\\

 Beside the fact that a 3D printer is needed for the project, a laser cutter is very useful for easy and fast prototyping. The material for the frame while be aluminum. The is because of the lightweight and sturdy properties. \\
 
 The frame that will support the 3D head also needs to be created. It needs to be flexible in design so that in the future it can be easily replaced or swap with a more traditional hotend or other designs. Futhermore it needs to able to withstand all the stresses and weight from the clay extruder.\\
 
 Lastly the motors that will be used are steppermotors. The reason for this is that we need a high level of accuracy. One of the most important aspect will be to generate enough torque. A normal steppermotor can't deliver enough torque to push clay through. A additional gearbox or gear conversion is needed to maintain the best combination of torque and speed. 

 	\begin{center}
Table 2. Morphological chart with part selection
\end{center}
 \begin{center}
 \begin{tabular}{|| c || c | c | c | c ||}
 
 \hline\hline
    \textit{Sub Functions} & \textit{Solutions} & \textit{Solutions}  & \textit{Solutions} & \textit{Solutions}   \\ [1.5ex]  
  \hline\hline
   
   \textit{3D head Type} & Stereolithography & Power Bed Fusion & \textcolor{green}{ Auger + Extruder} &  Hotend    \\
   \hline
    \textit{Motor} & Brush motor & \textcolor{green}{Stepper motor} & Linear motor & Brushless motor   \\
   \hline

 	\textit{Screw type} & \textcolor{green}{1 Screw} &  2 screw & x & x  \\
   \hline   
   	\textit{3D printhead material}   & \textcolor{green}{ ABS/PLA }& Metal casting & Aluminum & Wood     \\
   	\hline
   	\textit{Nozzle size}  & 0.6  & 0.8 & \textcolor{green}{ 1.2}  &\textcolor{green}{ 1.5 }  \\
   	\hline 
   	\textit{Controller}  & \textcolor{green}{ Mega + RAMPS } & Smoothieboard & Azteeg X5 GT  & RADDS   \\
   	\hline\hline 

 \end{tabular}
\end{center}  

\newpage

\section{Bills of Materials}

These items are necessary to create the 3D head and create a 3D design that works with clay  extruder.  

\begin{itemize}
	\item 3D Printhead
	\begin{itemize}
		\item Printed 3D Head(needs to be printed)
		\item Printed Base (needs to be printed)
		\item Nema 17 stepper motor 
		\item Stepper driver A4988
		\item Mega 2560 + RAMPS 1.4
		\item 1/2" Flat faucet washer
		\item 3/8" x 3/8" push fit male adapter
		\item Aluminum coupler 5mm
		\item Deck Screw	
		\item Cake decorating tips (nozzle)
		\item Acces to wood/metal for creating frames and support structures. 
	\end{itemize}
	\item Extruder
	\begin{itemize}
		\item 3D parts (needs to be printed)
		\item Nema 23 stepper motor 
		\item Stepper driver A4988
		\item Nema 23 gearbox: either 20:1 or 30:1
		\item Leadscrew
		\item Acces to wood/metal for creating frames and support structures. 		
	\end{itemize}	
\end{itemize}

\newpage

\section{Sources}

		University of Notre Dame.(2013). Initial Extruder Design. Accessed at 25 February 2019, from \\
	https://sites.nd.edu/3dp/2013/08/12/initial-extruder-design/\\
	
		The Italian Associationof Chemical Engineering.(2017). Design of 3D Metal FDM Printing Nozzle 	Based on Melt Forming. Accessed at 25 2019, from \\ 
	https://www.aidic.it/cet/17/59/013.pdf/ \\
	
		www.manufactur3dmag.com.(2018). 7 Methods of Manufacturing Metal 3D Printing Powder. Accessed at 25 			February 2019, from \\
	https://manufactur3dmag.com/7-methods-manufacturing-metal-3d-printing-powder/\\
		
	www.engineersedge.com (2018). Screw Type Positive Displacement Pump . Accessed at 25 February 2019, from \\
	http://beta.briefideas.org/ideas/ae254dc0e368a1b2b87b4047109f9b59\\
	
	Colfax Fluid HandlingWhite Paper.(2011). What’s a screw pump? Understanding the unique characteristics and operating principles of 1, 2 and 3 screw pumps. Accessed at  25 February 2019, from \\
	http://empoweringpumps.com/wp-content/uploads/sites/3/2013/05/What-is-a-screw-pump.pdf\\
	
	www.engineersedge.com (2018). Screw Type Positive Displacement Pump . Accessed at 25 February 2019, from \\
	http://beta.briefideas.org/ideas/ae254dc0e368a1b2b87b4047109f9b59\\
	
		Ali Morris, Dezeen.com .(2018). Dutch designers convert algae into bioplastic for 3D printing. Accessed at 25 February 2019, from \\
	https://www.dezeen.com/2017/12/04/dutch-designers-eric-klarenbeek-maartje-dros-convert-algae-biopolymer-3d-printing-good-design-bad-world/	\\
	
		www.3ders.org.(2013). 3D printed 'Mycelium Chair' made from water, straw and fungus. Accessed at 25 February 2019, from \\
	https://www.3ders.org/articles/20131021-3d-printed-mycelium-chair-made-from-water-straw-and-fungus.html\\
	
		3D Printlife.(2018). ALGA™ Algae Based PLA. Accessed at 25 February 2019, from \\
	https://www.3dprintlife.com/http/www3dprintlifecom/filaments/alga\\
	
	Wageningen University \& Research.(2016). MACROFUELS: Macro-algae as a sustainable source for biofuels. Accessed at 25 February 2019, from \\
	https://www.wur.nl/nl/project/MACROFUELS-Macro-algae-as-a-sustainable-source-for-biofuels.html\\
	
	Menno\-Jan\_Rietema\, University of Twente.(2015). Design of a prototype machine for 3D printing with continous fibre. Accessed at 25 February 2019, from \\
	https://essay.utwente.nl/71622/1/Thesis\_Menno\-Jan\_Rietema.pdf\\
	
	Tom Landerhaus.(2018). Bricoleur Clay Extruder, Open Source. Accessed at 25 February 2019, from \\
	https://www.thingiverse.com/thing:1413969\\
	
		Bryan Cera.(2018). Bricoleur Clay Extruder. Accessed at 25 February 2019, from \\ 
	https://www.thingiverse.com/thing:1413969\\
	
\newpage	
	 	Wikipedia(2018). Clay. Accessed at 25 February 2019, from \\ 
	https://en.wikipedia.org/wiki/Clay\\
	
	 	Formlabs.com. (2018). FDM vs SLA vs SLS . Accessed at 25 February 2019, from \\ 
     https://formlabs.com/blog/fdm-vs-sla-vs-sls-how-to-choose-the-right-3d-printing-technology/\\
	
		Formlabs.com.(2018). Ultimate guide tot stereolithography . Accessed at 25 February 2019, from \\ 
	https://formlabs.com/blog/ultimate-guide-to-stereolithography-sla-3d-printing/\\
	
		Wikipedia.(2018). Photopolymer. Accessed at 25 February 2019, from \\ 
	https://en.wikipedia.org/wiki/Photopolymer\\
	
		Loughborough University.(2018). Powder Bed Fusion . Accessed at 25 February 2019, from \\ 
	https://www.lboro.ac.uk/research/amrg/about/the7categoriesofadditivemanufacturing/powderbedfusion/\\

	    M. Entezarian F. Allaire P. TsantrizosR. A.L.DrewBryan.(1996). Plasma atomization: A new process for the production of fine, spherical powders. Accessed at 25 February 2019, from \\ 
	https://link.springer.com/article/10.1007/BF03222969\\
	
		Motioncontroltips.com (2017).  How can brush wear in DC motors be minimized?. Accessed at 25 February 2019, from \\ 
	https://www.motioncontroltips.com/faq-how-can-brush-wear-in-dc-motors-be-minimized/\\

		Motioncontroltips.com (2017).  linear motor how it works. Accessed at 25 February 2019, from \\ 	
	https://www.motioncontrol.com/products/linear-motor-how-it-works/\\
	
	www.applied-motion.com (2018). What do nema suzes meen. Accessed at 25 February 2019, from \\ 
     https://www.applied-motion.com/news/2015/10/what-do-nema-sizes-mean\\
	
	www.applied-motion.com (2018). Gear stacks. Accessed at 25 February 2019, from \\ 
	https://www.applied-motion.com/news/2015/10/stacks-stacks

\end{document}

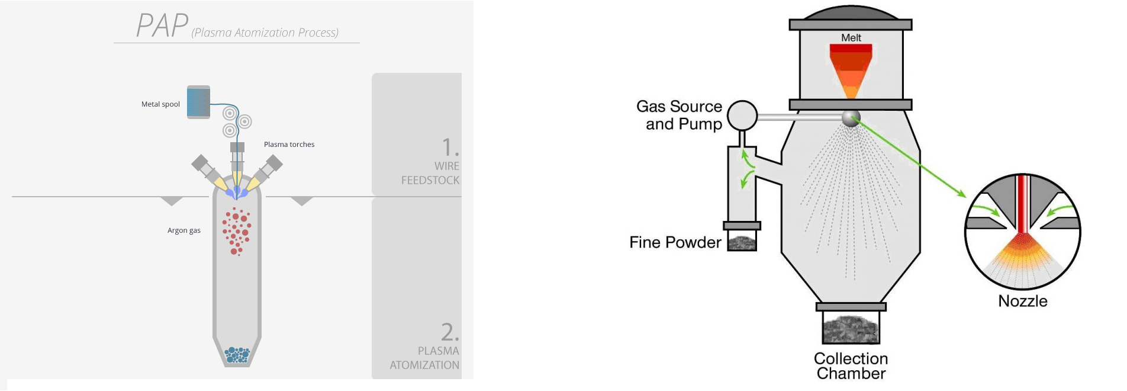
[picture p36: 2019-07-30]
Documentation/Thomas/Playa printer Latex onderzoek/build/combinedgasplasma.png

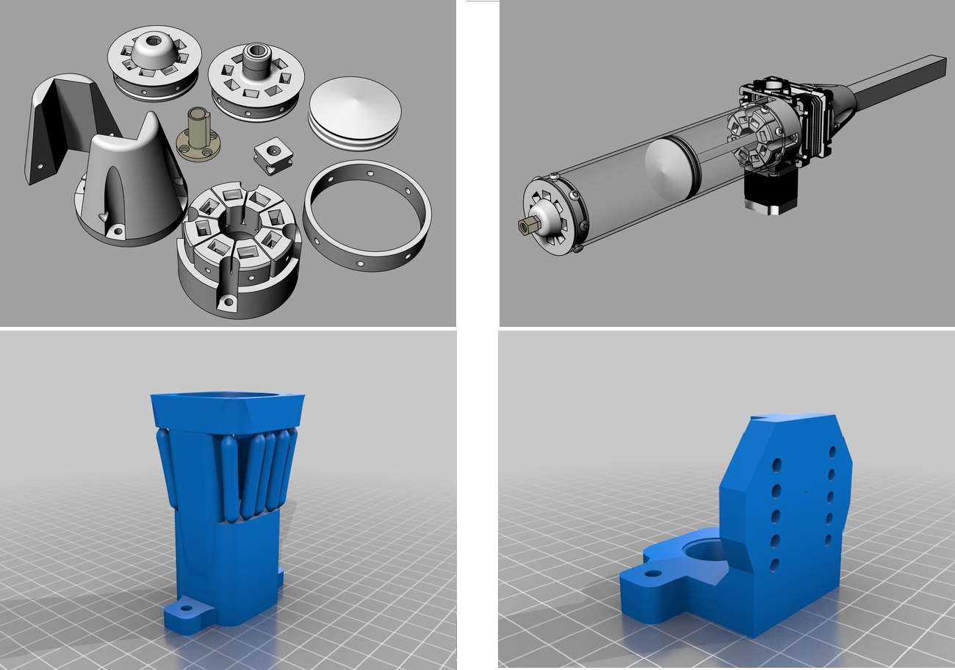
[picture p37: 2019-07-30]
Documentation/Thomas/Playa printer Latex onderzoek/build/3DPrintsTotal.png

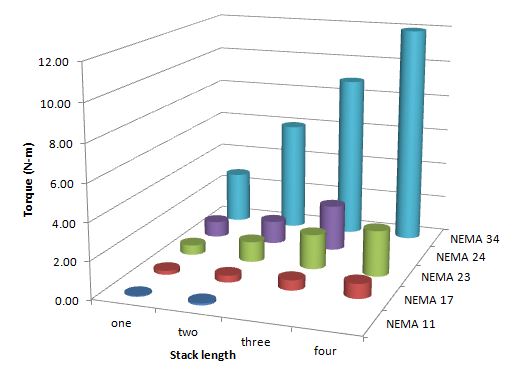
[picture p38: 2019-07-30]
Documentation/Thomas/Playa printer Latex onderzoek/build/torgue.png

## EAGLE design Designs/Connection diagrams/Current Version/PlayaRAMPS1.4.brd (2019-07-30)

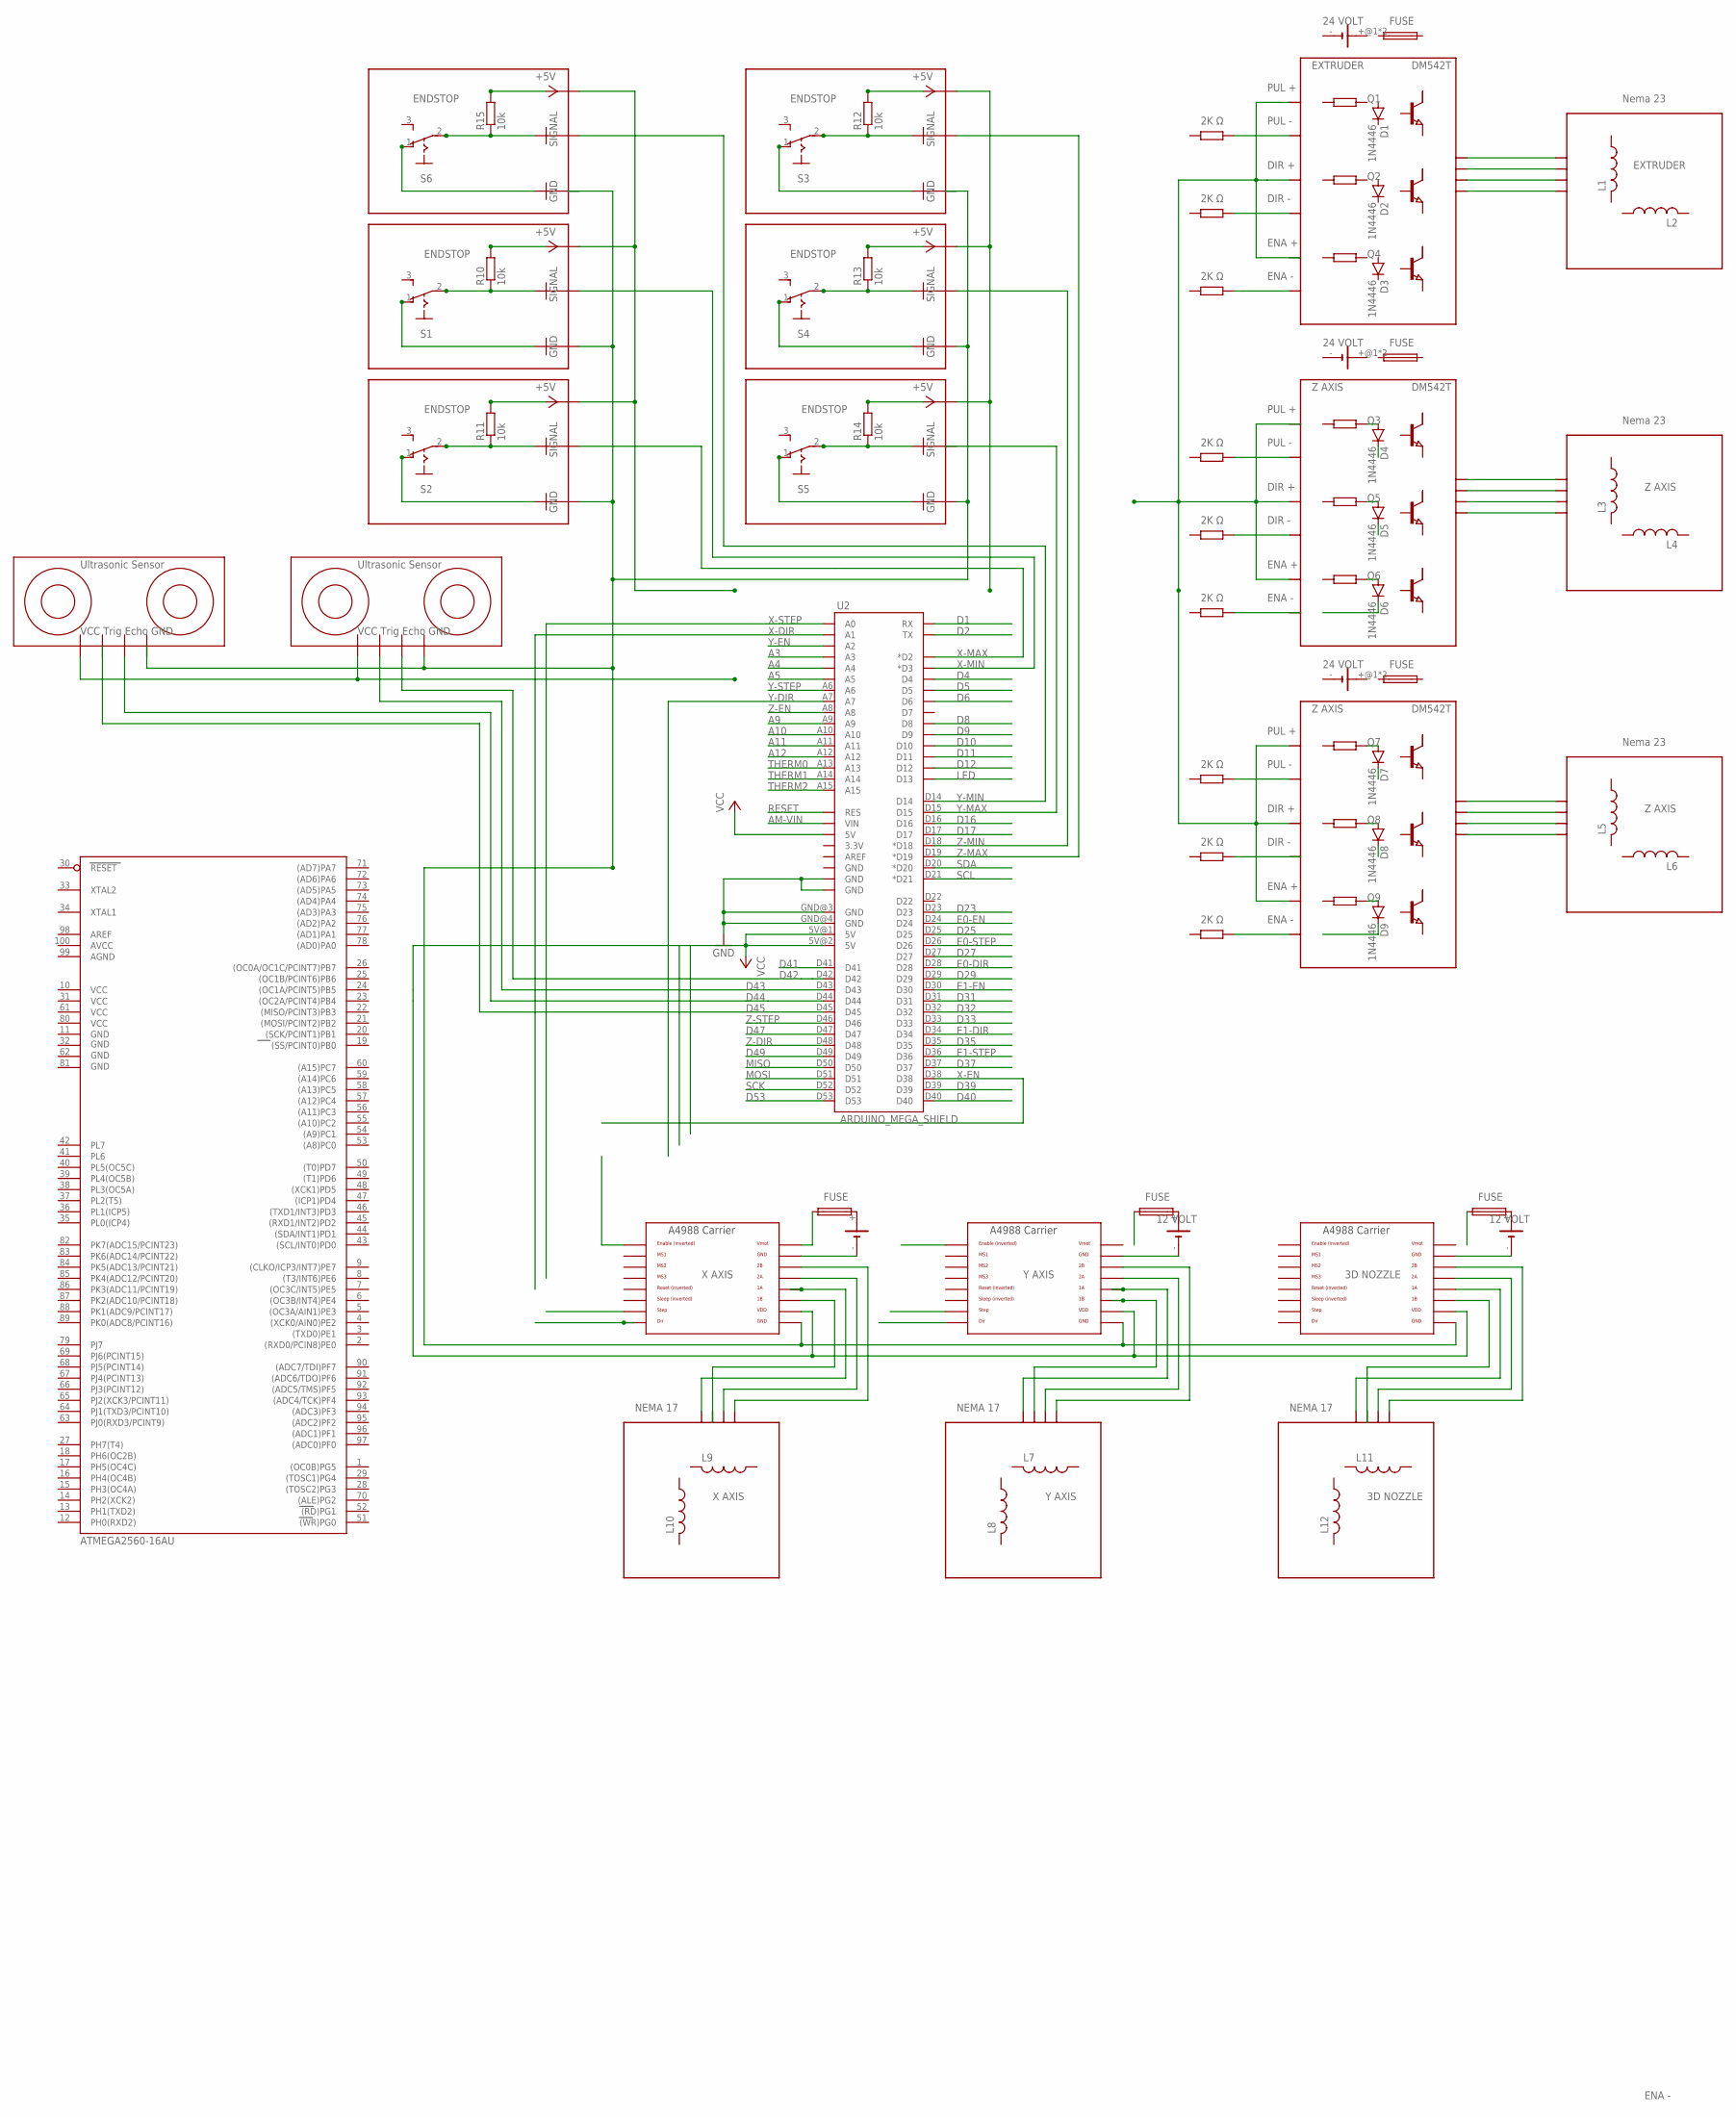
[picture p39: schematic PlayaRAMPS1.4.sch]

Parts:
D1, D2, D3, D4, D5, D6, D7, D8, D9: 1N4446; DO35-10
F1, F2, F3, F4, F5, F6: QPL
G1, G5, G6: 10MM_SM_COIN_CELL_CLIP
G2, G3, G4: CH291-1220LF
IC3: ATMEGA2560-16AU; TQFP100
L1, L2, L3, L4, L5, L6, L7, L8, L9, L10, L11, L12: L-US0204/5; 0204/5
Q1, Q2, Q3, Q4, Q5, Q6, Q7, Q8, Q9: NPN-TRANSISTIOR-2COLSOT143; SOT143
R10, R11, R12, R13, R14, R15: 10k; 0204/7
R16, R17, R18, R19, R20, R21, R22, R23, R24: R; R0805
S1, S2, S3, S4, S5, S6: 255SB
U2: ARDUINO_MEGA_SHIELD
X1, X2, X3: A4988BREAKOUT

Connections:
+5V: R10.2, R11.2, R12.2, R13.2, R14.2, R15.2
A3: U2.A3
A4: U2.A4
A5: U2.A5
A9: U2.A9
A10: U2.A10
A11: U2.A11
A12: U2.A12
AGND: IC3.99 (AGND)
AM-VIN: U2.VIN
AVCC: IC3.100 (AVCC)
D1: U2.RX
D2: U2.TX
D4: U2.D4
D5: U2.D5
D6: U2.D6
D8: U2.D8
D9: U2.D9
D10: U2.D10
D11: U2.D11
D12: U2.D12
D16: U2.D16
D17: U2.D17
D23: U2.D23
D25: U2.D25
D27: U2.D27
D29: U2.D29
D31: U2.D31
D32: U2.D32
D33: U2.D33
D35: U2.D35
D37: U2.D37
D39: U2.D39
D40: U2.D40
D41: U2.D41
D42: U2.D42
D43: U2.D43
D44: U2.D44
D45: U2.D45
D47: U2.D47
D49: U2.D49
D53: U2.D53
E0-DIR: U2.D28
E0-EN: U2.D24
E0-STEP: U2.D26
E1-DIR: U2.D34
E1-EN: U2.D30
E1-STEP: U2.D36
GND: IC3.11 (GND), R10.1, R11.1, R12.1, R13.1, R14.1, R15.1, S1.1 (O), S1.2, S2.1 (O), S2.2, S3.1 (O), S3.2, S4.1 (O), S4.2, S5.1 (O), S5.2, S6.1 (O), S6.2, U2.GND@0 (GND), U2.GND@1 (GND), U2.GND@3 (GND), U2.GND@4 (GND)
GND1: IC3.32 (GND1)
GND2: IC3.62 (GND2)
GND3: IC3.81 (GND3)
LED: U2.D13
MISO: U2.D50
MOSI: U2.D51
unnamed: F1.2, G2.+
unnamed: F2.2, G3.+
unnamed: F3.2, G4.+
unnamed: G4.-, X3.GND
unnamed: G3.-, X2.GND
unnamed: G2.-, X1.GND
unnamed: F1.1, X1.VMOT
unnamed: X1.GND@0 (GND), X2.GND@0 (GND), X3.GND@0 (GND)
RESET: U2.RES
SCK: U2.D52
SCL: U2.D21 (*D21)
SDA: U2.D20 (*D20)
THERM0: U2.A13
THERM1: U2.A14
THERM2: U2.A15
VCC: IC3.10 (VCC), U2.5V@0 (5V), U2.5V@1 (5V), U2.5V@2 (5V), X1.VDD, X2.VDD, X3.VDD
VCC1: IC3.31 (VCC1)
VCC2: IC3.61 (VCC2)
VCC3: IC3.80 (VCC3)
VMOT: X2.VMOT, X3.VMOT
X-DIR: U2.A1
X-DIR1: X1.DIR
X-EN: U2.D38
X-EN1: X1.EN
X-MAX: U2.D2 (*D2)
X-MIN: U2.D3 (*D3)
X-STEP: U2.A0
X-STEP1: X1.STEP
Y-DIR: U2.A7
Y-DIR1: X2.DIR
Y-EN: U2.A2
Y-MAX: U2.D15
Y-MIN: U2.D14
Y-STEP: U2.A6
Z-DIR: U2.D48
Z-EN: U2.A8
Z-MAX: U2.D19 (*D19)
Z-MIN: U2.D18 (*D18)
Z-STEP: U2.D46

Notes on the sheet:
ENA -
NEMA 17
PUL -
PUL +
DIR +
DIR -
ENA +
12 VOLT
X AXIS
Y AXIS
3D NOZZLE
2K Ω
Ultrasonic Sensor
VCC Trig Echo GND
FUSE
Nema 23
DM542T
24 VOLT
Z AXIS
EXTRUDER
ENDSTOP

Board: 2 copper layers, 68 parts (0 on the bottom side), 12 nets, no tracks yet.

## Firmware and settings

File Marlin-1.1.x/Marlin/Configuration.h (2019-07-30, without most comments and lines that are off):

#define CONFIGURATION_H
#define CONFIGURATION_H_VERSION 010109
#define STRING_CONFIG_H_AUTHOR "(none, default config)" // Who made the changes.
#define SHOW_BOOTSCREEN
#define STRING_SPLASH_LINE1 SHORT_BUILD_VERSION // will be shown during bootup in line 1
#define STRING_SPLASH_LINE2 WEBSITE_URL         // will be shown during bootup in line 2
#define SERIAL_PORT 0
#define BAUDRATE 115200
  #define MOTHERBOARD BOARD_RAMPS_14_EFB
#define MACHINE_UUID "6b82af56-c7b9-41e2-99fa-451697f835ac"
#define EXTRUDERS 1
#define DEFAULT_NOMINAL_FILAMENT_DIA 3.0
#define POWER_SUPPLY 0
#define TEMP_SENSOR_0 1
#define TEMP_SENSOR_1 0
#define TEMP_SENSOR_2 0
#define TEMP_SENSOR_3 0
#define TEMP_SENSOR_4 0
#define TEMP_SENSOR_BED 0
#define TEMP_SENSOR_CHAMBER 0
#define DUMMY_THERMISTOR_998_VALUE 25
#define DUMMY_THERMISTOR_999_VALUE 100
#define MAX_REDUNDANT_TEMP_SENSOR_DIFF 10
#define TEMP_RESIDENCY_TIME 10  // (seconds)
#define TEMP_HYSTERESIS 3       // (degC) range of +/- temperatures considered "close" to the target one
#define TEMP_WINDOW     1       // (degC) Window around target to start the residency timer x degC early.
#define TEMP_BED_RESIDENCY_TIME 10  // (seconds)
#define TEMP_BED_HYSTERESIS 3       // (degC) range of +/- temperatures considered "close" to the target one
#define TEMP_BED_WINDOW     1       // (degC) Window around target to start the residency timer x degC early.
#define HEATER_0_MINTEMP 5
#define HEATER_1_MINTEMP 5
#define HEATER_2_MINTEMP 5
#define HEATER_3_MINTEMP 5
#define HEATER_4_MINTEMP 5
#define BED_MINTEMP 5
#define HEATER_0_MAXTEMP 275
#define HEATER_1_MAXTEMP 275
#define HEATER_2_MAXTEMP 275
#define HEATER_3_MAXTEMP 275
#define HEATER_4_MAXTEMP 275
#define BED_MAXTEMP 150
#define PIDTEMP
#define BANG_MAX 255     // Limits current to nozzle while in bang-bang mode; 255=full current
#define PID_MAX BANG_MAX // Limits current to nozzle while PID is active (see PID_FUNCTIONAL_RANGE below); 255=full current
#define PID_K1 0.95      // Smoothing factor within any PID loop
  #define PID_FUNCTIONAL_RANGE 10 // If the temperature difference between the target temperature and the actual temperature
  #define DEFAULT_Kp 22.2
  #define DEFAULT_Ki 1.08
  #define DEFAULT_Kd 114
#define MAX_BED_POWER 255 // limits duty cycle to bed; 255=full current
#define PREVENT_COLD_EXTRUSION
#define EXTRUDE_MINTEMP 170
#define PREVENT_LENGTHY_EXTRUDE
#define EXTRUDE_MAXLENGTH 200
#define THERMAL_PROTECTION_HOTENDS // Enable thermal protection for all extruders
#define THERMAL_PROTECTION_BED     // Enable thermal protection for the heated bed
#define COREYX
#define USE_XMIN_PLUG
#define USE_YMIN_PLUG
#define USE_ZMIN_PLUG
#define ENDSTOPPULLUPS
#define X_MIN_ENDSTOP_INVERTING true // set to true to invert the logic of the endstop.
#define Y_MIN_ENDSTOP_INVERTING true // set to true to invert the logic of the endstop.
#define Z_MIN_ENDSTOP_INVERTING true // set to true to invert the logic of the endstop.
#define X_MAX_ENDSTOP_INVERTING false // set to true to invert the logic of the endstop.
#define Y_MAX_ENDSTOP_INVERTING false // set to true to invert the logic of the endstop.
#define Z_MAX_ENDSTOP_INVERTING false // set to true to invert the logic of the endstop.
#define Z_MIN_PROBE_ENDSTOP_INVERTING false // set to true to invert the logic of the probe.
#define DEFAULT_AXIS_STEPS_PER_UNIT   { 80, 128, 4000, 500 }
#define DEFAULT_MAX_FEEDRATE          { 300, 300, 5, 25 }
#define DEFAULT_MAX_ACCELERATION      { 3000, 3000, 100, 10000 }
#define DEFAULT_ACCELERATION          3000    // X, Y, Z and E acceleration for printing moves
#define DEFAULT_RETRACT_ACCELERATION  3000    // E acceleration for retracts
#define DEFAULT_TRAVEL_ACCELERATION   3000    // X, Y, Z acceleration for travel (non printing) moves
#define DEFAULT_XJERK                 10.0
#define DEFAULT_YJERK                 10.0
#define DEFAULT_ZJERK                  0.3
#define DEFAULT_EJERK                  5.0
#define Z_MIN_PROBE_USES_Z_MIN_ENDSTOP_PIN
#define X_PROBE_OFFSET_FROM_EXTRUDER 10  // X offset: -left  +right  [of the nozzle]
#define Y_PROBE_OFFSET_FROM_EXTRUDER 10  // Y offset: -front +behind [the nozzle]
#define Z_PROBE_OFFSET_FROM_EXTRUDER 0   // Z offset: -below +above  [the nozzle]
#define MIN_PROBE_EDGE 10
#define XY_PROBE_SPEED 8000
#define Z_PROBE_SPEED_FAST HOMING_FEEDRATE_Z
#define Z_PROBE_SPEED_SLOW (Z_PROBE_SPEED_FAST / 2)
#define Z_CLEARANCE_DEPLOY_PROBE   10 // Z Clearance for Deploy/Stow
#define Z_CLEARANCE_BETWEEN_PROBES  5 // Z Clearance between probe points
#define Z_CLEARANCE_MULTI_PROBE     5 // Z Clearance between multiple probes
#define Z_PROBE_LOW_POINT          -2 // Farthest distance below the trigger-point to go before stopping
#define Z_PROBE_OFFSET_RANGE_MIN -20
#define Z_PROBE_OFFSET_RANGE_MAX 20
#define X_ENABLE_ON 0
#define Y_ENABLE_ON 0
#define Z_ENABLE_ON 0
#define E_ENABLE_ON 0 // For all extruders
#define DISABLE_X false
#define DISABLE_Y false
#define DISABLE_Z false
#define DISABLE_E false // For all extruders
#define DISABLE_INACTIVE_EXTRUDER true // Keep only the active extruder enabled.
#define INVERT_X_DIR true
#define INVERT_Y_DIR true
#define INVERT_Z_DIR false
#define INVERT_E0_DIR false
#define INVERT_E1_DIR false
#define INVERT_E2_DIR false
#define INVERT_E3_DIR false
#define INVERT_E4_DIR false
#define X_HOME_DIR -1
#define Y_HOME_DIR -1
#define Z_HOME_DIR -1
#define X_BED_SIZE 3000
#define Y_BED_SIZE 3000
#define X_MIN_POS 0
#define Y_MIN_POS 0
#define Z_MIN_POS 0
#define X_MAX_POS X_BED_SIZE
#define Y_MAX_POS Y_BED_SIZE
#define Z_MAX_POS 200
#define MIN_SOFTWARE_ENDSTOPS
  #define MIN_SOFTWARE_ENDSTOP_X
  #define MIN_SOFTWARE_ENDSTOP_Y
  #define MIN_SOFTWARE_ENDSTOP_Z
#define MAX_SOFTWARE_ENDSTOPS
  #define MAX_SOFTWARE_ENDSTOP_X
  #define MAX_SOFTWARE_ENDSTOP_Y
  #define MAX_SOFTWARE_ENDSTOP_Z
#define HOMING_FEEDRATE_XY (50*60)
#define HOMING_FEEDRATE_Z  (4*60)
#define EEPROM_SETTINGS // Enable for M500 and M501 commands
#define EEPROM_CHITCHAT   // Give feedback on EEPROM commands. Disable to save PROGMEM.
#define HOST_KEEPALIVE_FEATURE        // Disable this if your host doesn't like keepalive messages
#define DEFAULT_KEEPALIVE_INTERVAL 2  // Number of seconds between "busy" messages. Set with M113.
#define BUSY_WHILE_HEATING            // Some hosts require "busy" messages even during heating
#define PREHEAT_1_TEMP_HOTEND 180
#define PREHEAT_1_TEMP_BED     70
#define PREHEAT_1_FAN_SPEED     0 // Value from 0 to 255
#define PREHEAT_2_TEMP_HOTEND 240
#define PREHEAT_2_TEMP_BED    110
#define PREHEAT_2_FAN_SPEED     0 // Value from 0 to 255
#define PRINTJOB_TIMER_AUTOSTART
#define LCD_LANGUAGE en
#define DISPLAY_CHARSET_HD44780 JAPANESE
#define NO_LCD_MENUS
#define ULTRA_LCD
#define LCM1602
#define SOFT_PWM_SCALE 0
#define SERVO_DELAY { 300 }

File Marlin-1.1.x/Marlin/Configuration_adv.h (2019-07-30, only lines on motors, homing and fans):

#define E0_AUTO_FAN_PIN -1
#define E1_AUTO_FAN_PIN -1
#define E2_AUTO_FAN_PIN -1
#define E3_AUTO_FAN_PIN -1
#define E4_AUTO_FAN_PIN -1
#define CHAMBER_AUTO_FAN_PIN -1
#define X_HOME_BUMP_MM 5
#define Y_HOME_BUMP_MM 5
#define Z_HOME_BUMP_MM 2
#define HOMING_BUMP_DIVISOR { 2, 2, 4 }  // Re-Bump Speed Divisor (Divides the Homing Feedrate)
#define MICROSTEP_MODES { 16, 16, 16, 16, 16 } // [1,2,4,8,16]
#define DIGIPOT_I2C_MOTOR_CURRENTS { 1.0, 1.0, 1.0, 1.0, 1.0, 1.0, 1.0, 1.0 }  //  AZTEEG_X3_PRO

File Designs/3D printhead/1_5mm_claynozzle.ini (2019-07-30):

[profile]
layer_height = 1
wall_thickness = 3
retraction_enable = True
solid_layer_thickness = 3
fill_density = 25
perimeter_before_infill = True
nozzle_size = 1.5
print_speed = 40
print_temperature = 0
print_temperature2 = 0
print_temperature3 = 0
print_temperature4 = 0
print_temperature5 = 0
print_bed_temperature = 0
support = None
platform_adhesion = None
support_dual_extrusion = Both
wipe_tower = False
wipe_tower_volume = 15
ooze_shield = False
filament_diameter = 2.6
filament_diameter2 = 0
filament_diameter3 = 0
filament_diameter4 = 0
filament_diameter5 = 0
filament_flow = 100.0
retraction_speed = 40
retraction_amount = 1
retraction_dual_amount = 16.5
retraction_min_travel = 1.5
retraction_combing = All
retraction_minimal_extrusion = 0.02
retraction_hop = 0.0
bottom_thickness = 0.3
layer0_width_factor = 100
object_sink = 0.0
overlap_dual = 0.15
travel_speed = 150
bottom_layer_speed = 20
infill_speed = 0.0
solidarea_speed = 0.0
inset0_speed = 0.0
insetx_speed = 0.0
cool_min_layer_time = 5
fan_enabled = True
skirt_line_count = 1
skirt_gap = 3.0
skirt_minimal_length = 150.0
fan_full_height = 0.5
fan_speed = 100
fan_speed_max = 100
cool_min_feedrate = 10
cool_head_lift = False
solid_top = True
solid_bottom = True
fill_overlap = 15
support_type = Lines
support_angle = 60
support_fill_rate = 15
support_xy_distance = 0.7
support_z_distance = 0.15
spiralize = False
simple_mode = False
brim_line_count = 20
raft_margin = 5.0
raft_line_spacing = 3.0
raft_base_thickness = 0.3
raft_base_linewidth = 1.0
raft_interface_thickness = 0.27
raft_interface_linewidth = 0.4
raft_airgap_all = 0.0
raft_airgap = 0.22
raft_surface_layers = 2
raft_surface_thickness = 0.27
raft_surface_linewidth = 0.4
fix_horrible_union_all_type_a = True
fix_horrible_union_all_type_b = False
fix_horrible_use_open_bits = False
fix_horrible_extensive_stitching = False
plugin_config = 
object_center_x = -1
object_center_y = -1
simplemodesettings = 
simplemodeprofile = Standard
simplemodematerial = PLA
simplemodematerialtype = Beginner

[alterations]
start.gcode = ;Sliced at: {day} {date} {time}
	;Basic settings: Layer height: {layer_height} Walls: {wall_thickness} Fill: {fill_density}
	;Print time: {print_time}
	;Filament used: {filament_amount}m {filament_weight}g
	;Filament cost: {filament_cost}
	;M190 S{print_bed_temperature} ;Uncomment to add your own bed temperature line
	;M109 S{print_temperature} ;Uncomment to add your own temperature line
	G21        ;metric values
	G90        ;absolute positioning
	M82        ;set extruder to absolute mode
	M107       ;start with the fan off
	G28 X0 Y0  ;move X/Y to min endstops
	G28 Z0     ;move Z to min endstops
	G1 Z15.0 F{travel_speed} ;move the platform down 15mm
	G92 E0                  ;zero the extruded length
	G1 F200 E3              ;extrude 3mm of feed stock
	G92 E0                  ;zero the extruded length again
	G1 F{travel_speed}
	;Put printing message on LCD screen
	M117 Printing...
end.gcode = ;End GCode
	M104 S0                     ;extruder heater off
	M140 S0                     ;heated bed heater off (if you have it)
	G91                                    ;relative positioning
	G1 E-1 F300                            ;retract the filament a bit before lifting the nozzle, to release some of the pressure
	G1 Z+0.5 E-5 X-20 Y-20 F{travel_speed} ;move Z up a bit and retract filament even more
	G28 X0 Y0                              ;move X/Y to min endstops, so the head is out of the way
	M84                         ;steppers off
	G90                         ;absolute positioning
	;{profile_string}
start2.gcode = ;Sliced at: {day} {date} {time}
	;Basic settings: Layer height: {layer_height} Walls: {wall_thickness} Fill: {fill_density}
	;Print time: {print_time}
	;Filament used: {filament_amount}m {filament_weight}g
	;Filament cost: {filament_cost}
	;M190 S{print_bed_temperature} ;Uncomment to add your own bed temperature line
	;M104 S{print_temperature} ;Uncomment to add your own temperature line
	;M109 T1 S{print_temperature2} ;Uncomment to add your own temperature line
	;M109 T0 S{print_temperature} ;Uncomment to add your own temperature line
	G21        ;metric values
	G90        ;absolute positioning
	M107       ;start with the fan off
	G28 X0 Y0  ;move X/Y to min endstops
	G28 Z0     ;move Z to min endstops
	G1 Z15.0 F{travel_speed} ;move the platform down 15mm
	T1                      ;Switch to the 2nd extruder
	G92 E0                  ;zero the extruded length
	G1 F200 E10             ;extrude 10mm of feed stock
	G92 E0                  ;zero the extruded length again
	G1 F200 E-{retraction_dual_amount}
	T0                      ;Switch to the first extruder
	G92 E0                  ;zero the extruded length
	G1 F200 E10             ;extrude 10mm of feed stock
	G92 E0                  ;zero the extruded length again
	G1 F{travel_speed}
	;Put printing message on LCD screen
	M117 Printing...
end2.gcode = ;End GCode
	M104 T0 S0                     ;extruder heater off
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

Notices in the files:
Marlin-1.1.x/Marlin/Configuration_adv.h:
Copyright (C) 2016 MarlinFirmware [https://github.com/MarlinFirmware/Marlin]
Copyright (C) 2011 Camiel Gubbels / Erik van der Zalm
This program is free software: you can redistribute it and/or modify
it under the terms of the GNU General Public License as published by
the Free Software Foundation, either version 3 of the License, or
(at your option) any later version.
